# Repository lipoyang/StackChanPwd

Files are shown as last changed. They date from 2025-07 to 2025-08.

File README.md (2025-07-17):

# Stack-chan Powerd
[日本語](./README_ja.md)

Stack-chan Powerd is a M5Stack-embedded super cute humanoid controller unit.

<!-- 動画埋め込み
## Video
[![代替テキスト](https://img.youtube.com/vi/nw4zOiLLuTk/0.jpg)](https://www.youtube.com/watch?v=nw4zOiLLuTk)
 -->
## System Overview
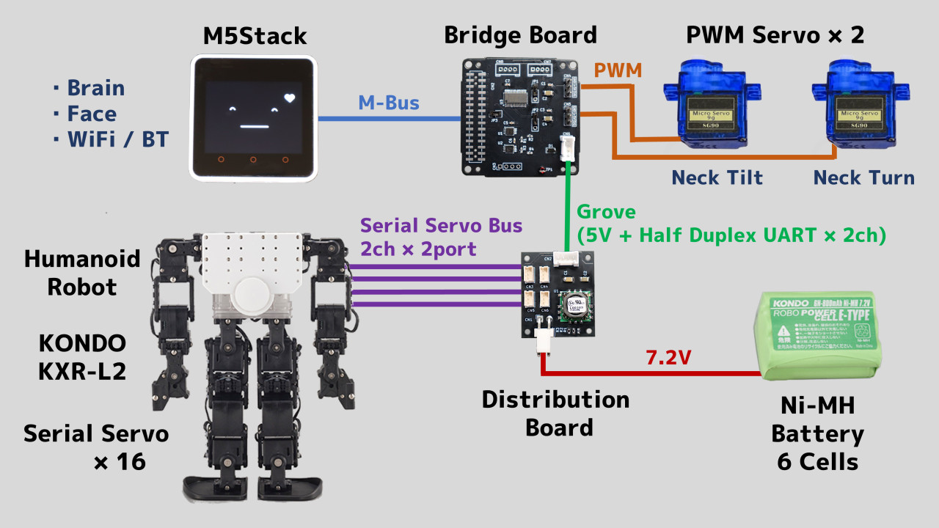
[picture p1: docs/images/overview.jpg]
System Overview


## Document
→ https://www.hackster.io/lipoyang/m5stack-as-a-humanoid-brain-b98882

## Files
* [firmware](./firmware/) : Source codes of the firmware.
* [case](./case/) : STEP and STL files of mechanical parts
* [boards](./boards/) : Schematics and PCB layout designs

## Original Work
This project is a derivative work inspired by Stack-chan. [Stack-chan](https://github.com/stack-chan/stack-chan) is the palm-sized super cute communication robot created by [Shinya Ishikawa](https://x.com/stack_chan).

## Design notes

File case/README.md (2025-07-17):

# Cumtom Mechanical Parts

These designs was forked from the original [Stack-chan case](https://github.com/stack-chan/stack-chan/tree/dev/v1.0/case).

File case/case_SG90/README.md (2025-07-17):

# Cumtom Mechanical Parts for SG90 and KXR-L2

* neck_SG90 : the neck base
* bracket_SG90_b / bracket_SG90_f : the neck bracket
* shell_SG90 : the skull shell

These designs was forked from the original [Stack-chan case](https://github.com/stack-chan/stack-chan/tree/dev/v1.0/case/case_SG90).

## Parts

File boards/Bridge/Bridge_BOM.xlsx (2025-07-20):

Reference | Qty | Part Number | Vendor | Description | DNP | Supplier | Supplier Code
C1,C3,C5,C6,C7 | 5 | 0.1uF (1608) | (generic) |  |  | - | -
C2,C4 | 2 | 100uF (3216) | (generic) |  |  | digikey | 490-GRM31CR61A107MEA8KCT-ND
CN1 | 1 | M-BUS 2x15 Pin Header (SMD) | M5Stack | M-BUS ピンヘッダ |  | スイッチサイエンス | 9591
CN2 | 1 | M-BUS 2x15 Pin Socket (SMD) | M5Stack | M-BUS ピンソケット | DNP | スイッチサイエンス | 9592
CN3 | 1 | 1x4 PinHeader | (generic) | マイク用 | DNP | - | -
CN4,CN5 | 2 | B3B-EH-A | JST | EH 3ピン (トップ型) |  | digikey | 455-B3B-EH-A-ND
CN6 | 1 | Grove (Top, through hole) | Seeed | 電源/サーボ用 |  | スイッチサイエンス | 1122
CN7,CN8 | 2 | Grove (Top, through hole) | Seeed | 拡張用 | DNP | スイッチサイエンス | 1122
D1 | 1 | SS2040FL | PANJIT |  |  | 秋月 | 102073
JP1,JP2,J3 | 3 | XX-2 | マックエイト |  |  | 秋月 | 110191
R1,R3 | 2 | 1kΩ | (generic) |  |  | - | -
R2,R4 | 2 | 100Ω | (generic) |  |  | - | -
TP1 | 1 | TEST-1 | マックエイト |  | DNP | 秋月 | 107591
U1 | 1 | 74LVC2G125DC (SM8) | TI | 0.65mm ピッチ |  | digikey | 296-SN74LVC2G125DCT3CT-ND
U2 | 1 | 74HCT2G125DP (8-TSSOP) | TI | 0.65mm ピッチ |  | digikey | 1727-3933-1-ND
U3 | 1 | PCA9685PW | NXP |  |  | digikey | 568-11925-1-ND

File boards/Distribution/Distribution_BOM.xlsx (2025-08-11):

Reference | Qty | Part Number | Vendor | Description | DNP | Supplier | Supplier Code
C1,C2 | 2 | 100uF (3216) | (generic) |  |  | digikey | 490-GRM31CR61A107MEA8KCT-ND
CN1 | 1 | B2PS-VH | JST | VH 2ピン (サイド型) |  | digikey | 455-B2PS-VH-ND
CN2 | 1 | Grove (Top, through hole) | Seeed |  |  | スイッチサイエンス | 1122
CN3,CN4,CN5,CN6 | 4 | B3B-ZR | JST | ZH 3ピン (トップ型) |  | digikey | 455-1658-ND
R1 | 1 | 1kΩ, class F | (generic) | ±1% |  | digikey | 10-ERJ-U03F1001VCT-ND
R2 | 1 | 220Ω, class F | (generic) | ±1% |  | digikey | 10-ERJ-U03F2200VCT-ND
R3 | 1 | 22Ω, class F | (generic) | ±1% |  | digikey | 10-ERJ-U03F22R0VCT-ND
U1 | 1 | OKL-T/3-W12N | Murata |  |  | digikey | 811-2072-1-ND

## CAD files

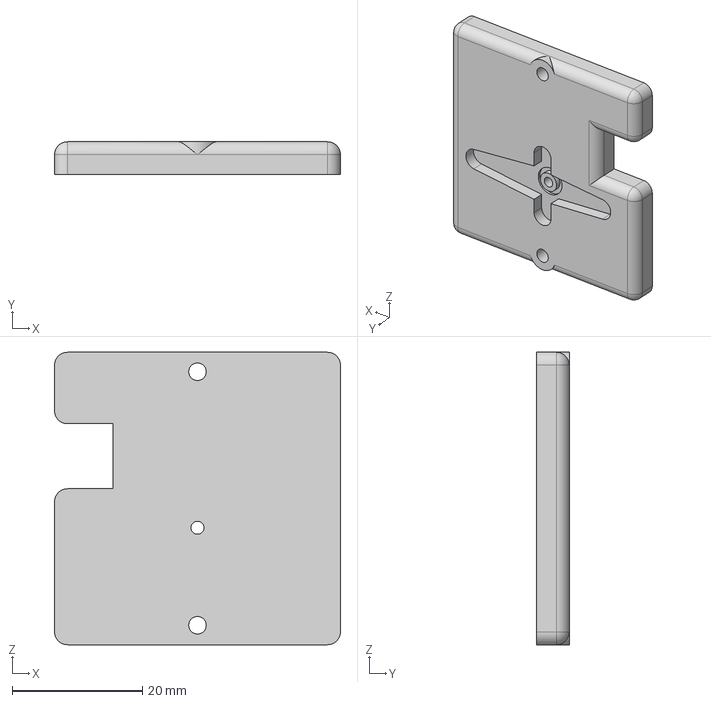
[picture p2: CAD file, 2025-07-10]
case/case_SG90/neck_SG90.step
44.0 x 5.00 x 45.0 mm

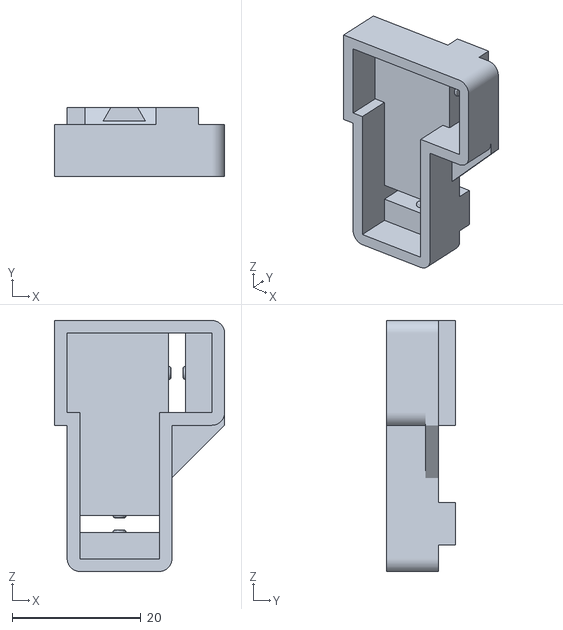
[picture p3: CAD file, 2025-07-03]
case/case_SG90/bracket_SG90_b.stl
26.5 x 10.7 x 39.1

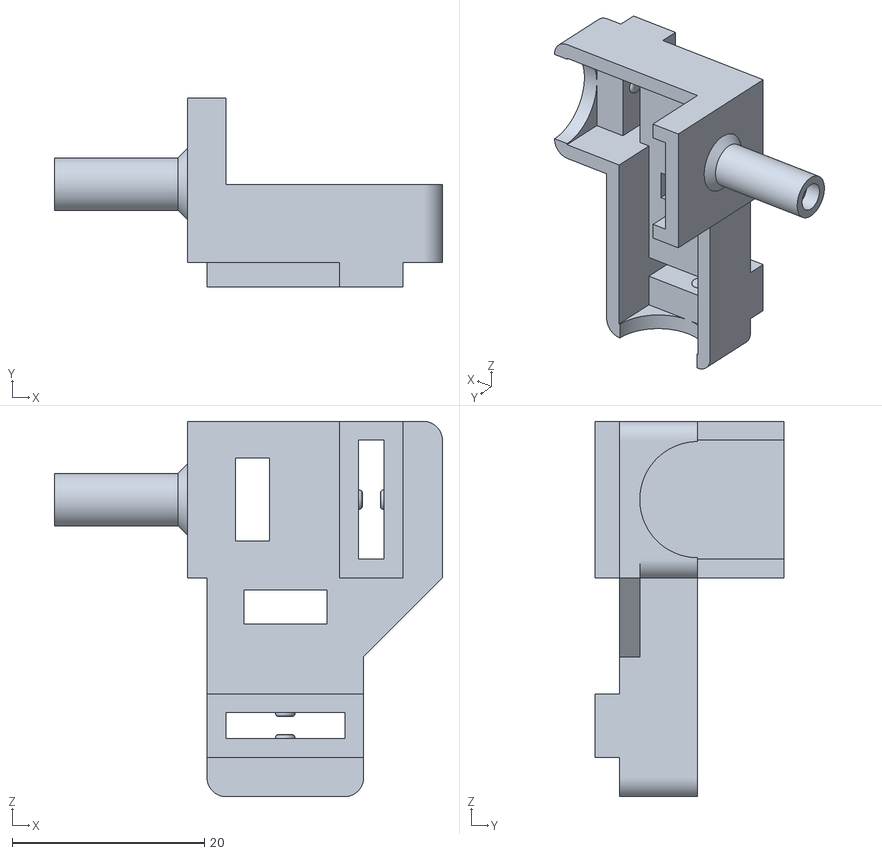
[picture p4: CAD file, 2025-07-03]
case/case_SG90/bracket_SG90_f.stl
40.4 x 19.7 x 39.1

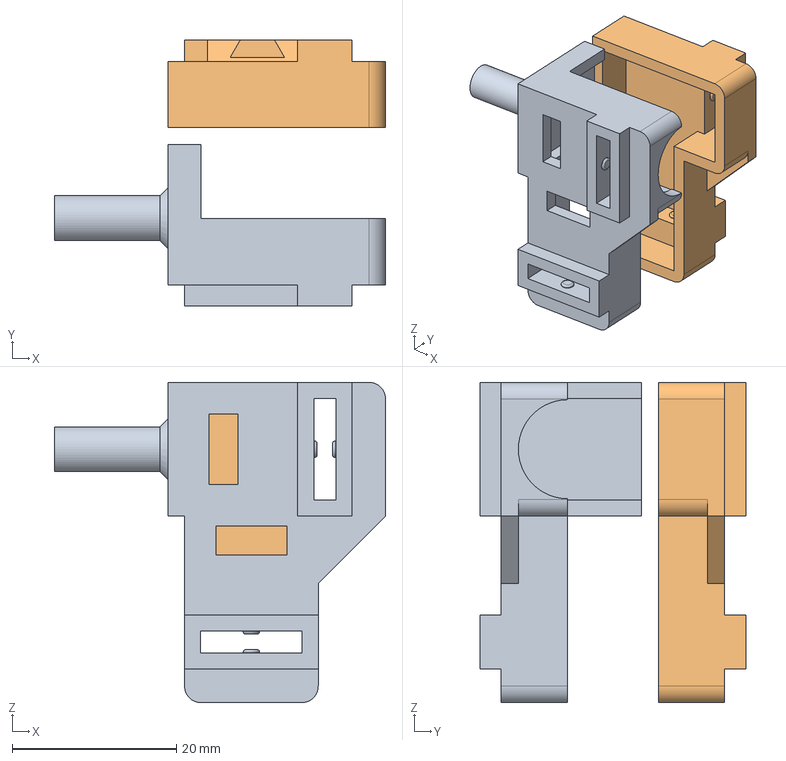
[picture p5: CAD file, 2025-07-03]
case/case_SG90/bracket_SG90.step
40.4 x 32.4 x 39.1 mm

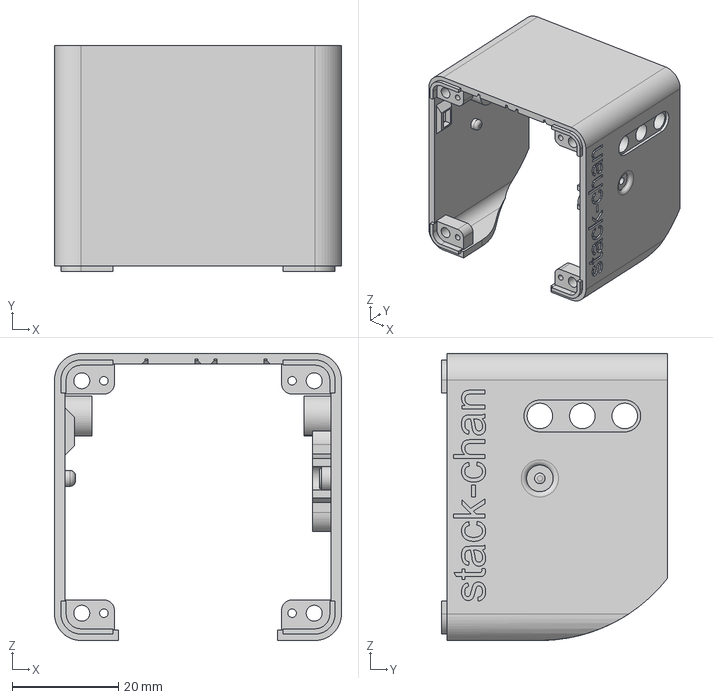
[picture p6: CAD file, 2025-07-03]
case/case_SG90/shell_SG90.step
54.0 x 42.5 x 54.0 mm

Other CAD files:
case/case_SG90/neck_SG90.stl
case/case_SG90/shell_SG90.stl

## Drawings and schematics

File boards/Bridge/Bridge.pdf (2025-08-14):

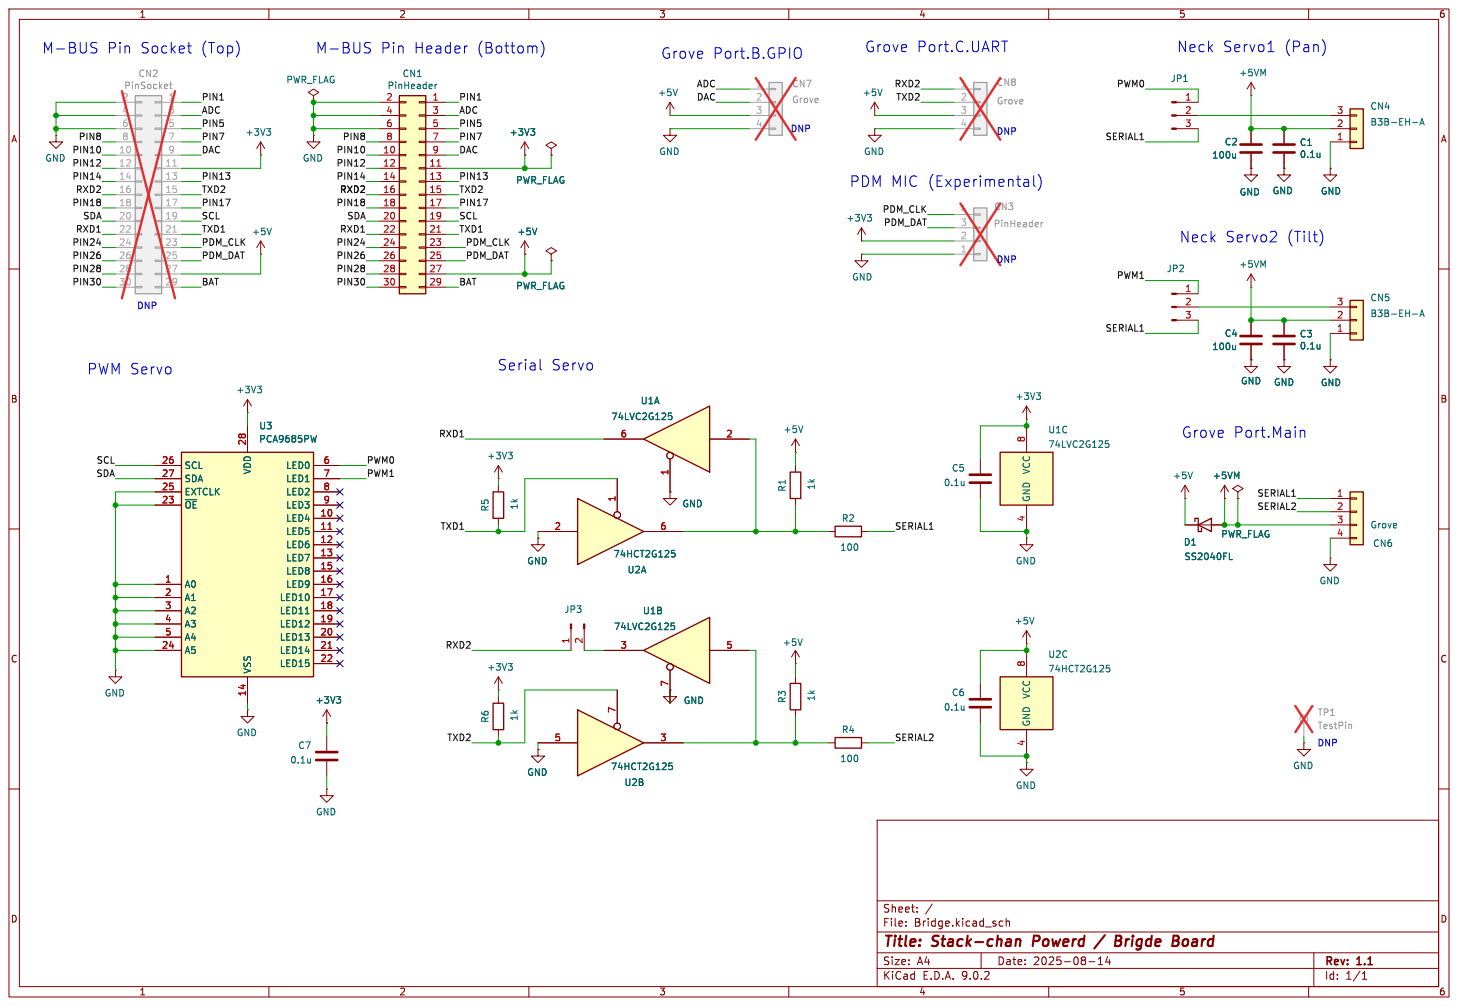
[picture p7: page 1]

M-BUS Pin Header (Bottom)

File: Bridge.kicad_sch Sheet: / GND

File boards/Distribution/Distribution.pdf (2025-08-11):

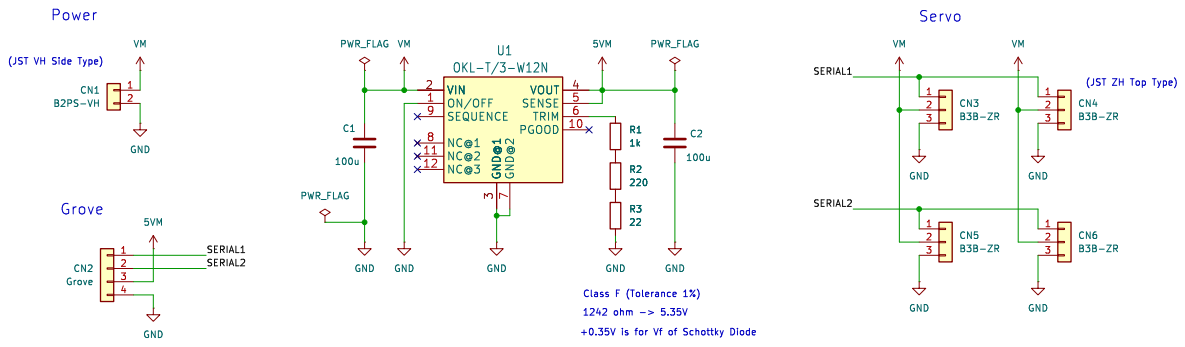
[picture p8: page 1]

(JST ZH Top Type) R3

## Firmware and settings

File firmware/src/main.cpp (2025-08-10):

#include <M5Unified.h>
#include "StackChanHead.h"
#include "GamePad_PS4.h"
#include "ICS.h"
#include "MotionController.h"
#include "Motion.h"
#include "common.h"

// シリアルポートのピン割り当て
#define PIN_RXD1 27
#define PIN_TXD1 19
#define PIN_RXD2 13
#define PIN_TXD2 14

// ICSサーボ
IcsController ics1(Serial1, PIN_RXD1, PIN_TXD1); // 右半身系統
IcsController ics2(Serial2, PIN_RXD2, PIN_TXD2); // 左半身系統
IcsServo servos[SERVO_NUM];

// モーションコントローラ
MotionController motionCtrl;

// トリム位置
const int16_t TRIM_POS[SERVO_NUM]={
//  肩P(右,左) 肩R         肘          腿R         腿P         膝           足首P       足首R
    1350,-1350,-2700,-2700,    0,    0,    0,    0, -250, -250,-2000,-2000,  520,  520,    0,    0
};

// ホームポジション
const int16_t HOME_POS[SERVO_NUM]={
//  肩P(右,左) 肩R         肘          腿R         腿P         膝           足首P       足首R
     400, -400,    0,    0,-1200,-1200,    0,    0,  150,  150,  300,  300,  150,  150,    0,    0
};

// ホームストレッチ
const uint8_t HOME_STRETCH[SERVO_NUM]={
//  肩P(右,左) 肩R         肘          腿R         腿P         膝           足首P       足首R
      20,   20,   20,   20,   65,   65,   65,   65,   65,   65,   65,   65,   65,   65,   65,   65
};

// 送信バッファ
static char txbuff[256];

// ゲームパッド (PS4コントローラ)
GamePad *gamepad;
GamePad_PS4 gamepad_ps4;
bool gamepad_connected = false;

// スタックチャン
using namespace m5avatar;
StackChanHead head;

// 初期化
void setup()
{
	auto cfg = M5.config();
  	M5.begin(cfg);

  	// スタックチャンの初期化
	head.begin();
  	head.setMicroMotion(false);

	Serial.begin(115200);
	Serial.println("StackChanPwd Start");
	
	// MACアドレスの確認用
  	uint8_t btmac[6];
  	esp_read_mac(btmac, ESP_MAC_BT);
  	Serial.printf("[Bluetooth] Mac Address = %02X:%02X:%02X:%02X:%02X:%02X\n", 
    	btmac[0], btmac[1], btmac[2], btmac[3], btmac[4], btmac[5]);

	// ICSサーボの初期化
	ics1.begin();
	ics2.begin();
	for(int i=0; i<(SERVO_NUM/2); i++){
		servos[i*2  ].attach(ics1, 1+i); // 右半身のサーボ
		servos[i*2+1].attach(ics2, 1+i); // 左半身のサーボ
	}
	
	// モーションコントローラの初期化
	motionCtrl.setServo(servos);
	motionCtrl.setTrim(TRIM_POS);
	motionCtrl.setHome(HOME_POS, HOME_STRETCH);
	motionCtrl.begin(M000::motion);

#if 0	// デバッグ用 (サーボの位置を確認)
	while(1){
		if(Serial.available() > 0){
			char c = Serial.read();
			if(c == 's') break;
		}
		for(int i=0;i<SERVO_NUM;i++){
			uint16_t pos = servos[i].getPosition();
			Serial.print(pos);Serial.print(" ");
		}
		Serial.println(" ");
		delay(1000);
	}
	Serial.println("Servo position check finished.");
#endif

	// ホームポジションに移動
	Serial.println("Stand Home position.");
	motionCtrl.standHome();

 	// ゲームパッドの初期化
	gamepad = &gamepad_ps4;
	gamepad->begin();

	// スタックチャンを居眠り状態に
	head.setBaseExpression(Expression::Sleepy);
	head.setExpression(Expression::Sleepy);
}

// メインループ
void loop()
{
	motionCtrl.loop();
	ics1.loop();
	ics2.loop();
	
	// ゲームパッド
  	if (gamepad->isConnected()) {
		if (!gamepad_connected) {
			Serial.println("GamePad connected.");
			gamepad_connected = true;
			head.setBaseExpression(Expression::Neutral);
			head.setExpression(Expression::Happy, 2000);
			head.setSpeachText("ゲームパッド接続", 2000);
			head.setMicroMotion(true);
		}
		// ゲームパッドのボタン状態を取得
		static uint32_t buttonFlag_prev = 0xFFFFFFFF;
    	uint32_t buttonFlag = gamepad->getButton();
		// ボタンフラグをモーションコントローラにセット
		motionCtrl.movButton(buttonFlag);
		if(buttonFlag != buttonFlag_prev) {
    		Serial.printf("Button Flag: 0x%08X\n", buttonFlag);
			//M5.Lcd.printf("Button Flag: 0x%08X\n", buttonFlag);
		}
		buttonFlag_prev = buttonFlag;

  	}else{
		if (gamepad_connected) {
			Serial.println("GamePad disconnected.");
			gamepad_connected = false;
			head.setBaseExpression(Expression::Sleepy);
			head.setExpression(Expression::Neutral, 2000);
			head.setSpeachText("ゲームパッド切断", 2000);
			head.setMicroMotion(false);
		}
	}

	// 開発用 (シリアル通信でのボタン入力)
	if(Serial.available() > 0){
		char c = Serial.read();
		if(c == '1') motionCtrl.setButton(BTN_L1);
		if(c == '2') motionCtrl.setButton(BTN_L2);
		if(c == '3') motionCtrl.setButton(BTN_R1);
		if(c == '4') motionCtrl.setButton(BTN_R2);
		if(c == 'a') motionCtrl.setButton(BTN_LEFT);
		if(c == 's') motionCtrl.setButton(BTN_DOWN);
		if(c == 'd') motionCtrl.setButton(BTN_UP);
		if(c == 'f') motionCtrl.setButton(BTN_RIGHT);
		if(c == 'h') motionCtrl.setButton(BTN_X);
		if(c == 'j') motionCtrl.setButton(BTN_A);
		if(c == 'k') motionCtrl.setButton(BTN_Y);
		if(c == 'l') motionCtrl.setButton(BTN_B);
		if(c == ' ') motionCtrl.clrButton(BTN_ALL);
	}
	
	// スタックチャン
	static const MotionData *motion_prev = M000::motion;
	const MotionData *motion = motionCtrl.getPresentMotion();
	if(motion != motion_prev) {
		motion_prev = motion;

		// モーションに応じてスタックチャンの表情を変える
		if((motion == M201::motion) || // パンチ左ストレート
		   (motion == M202::motion) || // パンチ右ストレート
		   (motion == M211::motion) || // A+←: パンチ左裏拳
		   (motion == M212::motion) || // A+→: パンチ右裏拳
		   (motion == M220::motion)    // A+↓: 防御
		){
			head.setExpression(Expression::Angry);
		}else{
			head.setExpression(Expression::Neutral);
		}
		// モーションに応じてスタックチャンの顔の向きを変える
		if       (motion == M003::motion) { // ←: 歩行左
			head.setPosition( 50, 0);
		} else if(motion == M004::motion) { // →: 歩行右
			head.setPosition(-50, 0);
		} else if(motion == M201::motion) {	// パンチ左ストレート
			head.setPosition( 25, 0);
		} else if(motion == M202::motion) {	// パンチ右ストレート
			head.setPosition(-25, 0);
		} else if(motion == M211::motion) { // A+←: パンチ左裏拳
			head.setPosition( 50, 0);
		} else if(motion == M212::motion) { // A+→: パンチ右裏拳
			head.setPosition(-50, 0);
		} else if(motion == M220::motion) { // A+↓: 防御
			head.setPosition(  0, -25);
		} else {
			head.setPosition(  0, 0);
		}
		// モーションに応じてスタックチャンの不随意運動を有効/無効にする
		if(motion == M000::motion){
			head.setMicroMotion(true);
		}else{
			head.setMicroMotion(false);
		}
	}
	head.loop();
}

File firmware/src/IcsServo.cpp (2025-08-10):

// KONDO ICS Serial Servo
// Based on ICS3.5

#include <stdio.h>
#include <string.h>
#include "IcsController.h"
#include "IcsServo.h"
#include "driver/uart.h" // optimize for M5Stack

/****************************************
 Constants of ICS Protocol
 ****************************************/

// CMD(command)
#define CMD_POSITION    0x80    // POSITION command
#define CMD_READ        0xA0    // READ command
#define CMD_WRITE       0xC0    // WRITE command
#define CMD_ID          0xE0    // ID command

#define CMD_MASK        0xE0    // bit mask of command
#define ID_MASK         0x1F    // bit mask of ID
#define MSB_MASK        0x7F    // bit mask of MSB

// SC(sub command) of READ/WRITE command
#define SC_EEPROM       0x00    // EEPROM
#define SC_STRETCH      0x01    // stretch
#define SC_SPEED        0x02    // speed
#define SC_CURRENT      0x03    // current
#define SC_TEMPERATURE  0x04    // temperature
#define SC_POSITION     0x05    // position (read only)

// SC(sub command) of ID command
#define SC_READ_ID      0x00    // read ID
#define SC_WRITE_ID     0x01    // write ID

// verify CMD
#define ICS_CMD_CHECK(rx, tx, tx_size) \
    ((rx[0] == tx[0]) && ((rx[tx_size+0] & MSB_MASK) == (tx[0] & MSB_MASK)))

// verify CMD (read ID command)
#define ICS_CMD_GET_ID_CHECK(rx, tx, tx_size) \
    ((rx[0] == tx[0]) && ((rx[tx_size+0] & CMD_MASK & MSB_MASK) == (CMD_ID & MSB_MASK)))

// verify SC
#define ICS_SC_CHECK(rx, tx, tx_size) \
    ((rx[1] == tx[1]) && (rx[tx_size+1] == tx[1]))

// verify DATA
#define ICS_DATA_CHECK(rx, tx, tx_size) \
    ((rx[2] == tx[2]) && (rx[tx_size+2] == tx[2]))

/****************************************
 Local Constants
 ****************************************/

// request flag bit
#define REQ_POSITION       0x01    // set & get position
#define REQ_CURRENT        0x02    // get current
#define REQ_TEMPERATURE    0x04    // get temperature

/****************************************
 Common API
 ****************************************/

// set ICS controller and servo ID
void IcsServo::attach(IcsController& controller, uint8_t id)
{
    this->controller = &controller;
    this->ID = id;
    
    // add this servo to servo chain
    if(controller.servoFirst == NULL)
    {
        controller.servoFirst = this;
        controller.servoLast = this;
        controller.servoNow = this;
    }
    else
    {
        controller.servoLast->next = this;
        controller.servoLast = this;
    }
    this->next = NULL;
}

/****************************************
 Synchronous API
 ****************************************/

// set & get position
// pos : target position
// return : current position
uint16_t IcsServo::setPosition(uint16_t pos)
{
    // command data
    uint8_t tx_data[3];
    tx_data[0] = CMD_POSITION | (ID & ID_MASK);// CMD
    tx_data[1] = (uint8_t)(pos >> 7) & 0x7F;   // POS_H
    tx_data[2] = (uint8_t)(pos & 0x7F);        // POS_L
    
    // send command and receive response
    uint8_t rx_data[3+3]={0};
    if(!this->transfer(tx_data, sizeof(tx_data), rx_data, sizeof(rx_data), 1)){
        return 0xFFFF;  // Error
    }
    
    // verify response data
    uint16_t retval;
    if(ICS_CMD_CHECK(rx_data, tx_data, 3)) // verify CMD
    {
        // current position
        retval = ((uint16_t)rx_data[3+1] << 7) | (uint16_t)rx_data[3+2];
    }else{
        retval = 0xFFFF;  // Error
    }
    return retval;
}

// read parameter (common routine)
// sc : sub command (type of parameter)
// return : value of parameter
uint8_t IcsServo::getParameter(uint8_t sc)
{
    // command data
    uint8_t tx_data[2];
    tx_data[0] = CMD_READ | (ID & ID_MASK); // CMD
    tx_data[1] = sc;  // SC
    
    // send command and receive response
    uint8_t rx_data[2+3]={0};
    if(!this->transfer(tx_data, sizeof(tx_data), rx_data, sizeof(rx_data), 1)){
        return 0xFF;  // Error
    }
    
    // verify response data
    uint8_t retval;
    if(   ICS_CMD_CHECK(rx_data, tx_data, 2) // verify CMD
       && ICS_SC_CHECK (rx_data, tx_data, 2)) // verify SC
    {
        // value of parameter
        retval = rx_data[2+2];
    }else{
        retval = 0xFF; // Error
    }
    return retval;
}

// get stretch
// return : stretch
uint8_t IcsServo::getStretch()
{
    return this->getParameter(SC_STRETCH);
}

// get speed
uint8_t IcsServo::getSpeed()
{
    return this->getParameter(SC_SPEED);
}

// get current
uint8_t IcsServo::getCurrent()
{
    return this->getParameter(SC_CURRENT);
}

// get temperature
uint8_t IcsServo::getTemperature()
{
    return this->getParameter(SC_TEMPERATURE);
}

// get position
uint16_t IcsServo::getPosition()
{
    // command data
    uint8_t tx_data[2];
    tx_data[0] = CMD_READ | (ID & ID_MASK); // CMD
    tx_data[1] = SC_POSITION;  // SC
    
    // send command and receive response
    uint8_t rx_data[2+4]={0};
    if(!this->transfer(tx_data, sizeof(tx_data), rx_data, sizeof(rx_data), 10)){
        return 0xFF;  // Error
    }
    
    // verify response data
    uint16_t retval;
    if(   ICS_CMD_CHECK(rx_data, tx_data, 2) // verify CMD
       && ICS_SC_CHECK (rx_data, tx_data, 2)) // verify SC
    {
        // value of parameter
        retval = ((uint16_t)rx_data[3+1] << 7) | (uint16_t)rx_data[3+2];
    }else{
        retval = 0xFFFF; // Error
    }
    return retval;
}


// write parameter (common routine)
// sc : sub command (type of parameter)
// value : value of parameter
// return : success or failure
bool IcsServo::setParameter(uint8_t sc, uint8_t value)
{
    // command data
    uint8_t tx_data[3];
    tx_data[0] = CMD_WRITE | (ID & ID_MASK); // CMD
    tx_data[1] = sc;    // SC
    tx_data[2] = value; // value of parameter
    
    // send command and receive response
    uint8_t rx_data[3+3]={0};
    if(!this->transfer(tx_data, sizeof(tx_data), rx_data, sizeof(rx_data), 1)){
        return false;  // Error
    }
    
    // verify response data
    bool retval;
    if(   ICS_CMD_CHECK (rx_data, tx_data, 3)  // verify CMD
       && ICS_SC_CHECK  (rx_data, tx_data, 3)  // verify SC
       && ICS_DATA_CHECK(rx_data, tx_data, 3)) // verify DATA
    {
        retval = true;
    }else{
        retval = false;
    }
    return retval;
}

// set stretch
// stretch : stretch
// return : success or failure
bool IcsServo::setStretch(uint8_t stretch)
{
    return this->setParameter(SC_STRETCH, stretch);
}

// set speed
// speed : speed
// return : success or failure
bool IcsServo::setSpeed(uint8_t speed)
{
    return this->setParameter(SC_SPEED, speed);
}

// set current limit
// current : current limit
// return : success or failure
bool IcsServo::setCurrent(uint8_t current)
{
    return this->setParameter(SC_CURRENT, current);
}

// set temperature limit
// temp : temprature limit
// return : success or failure
bool IcsServo::setTemperature(uint8_t temp)
{
    return this->setParameter(SC_TEMPERATURE, temp);
}
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

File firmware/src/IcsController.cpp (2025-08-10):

// KONDO ICS Serial Servo Controller
// Based on ICS3.5

#include <Arduino.h>
#include "IcsController.h"
#include "IcsServo.h"
#include "driver/uart.h" // optimize for M5Stack

/****************************************
 API
 ****************************************/

// constructor
// serial : serial port for ICS communication
IcsController::IcsController(HardwareSerial& serial, int rxPin, int txPin)
{
    this->serial = &serial;
    this->rxPin = rxPin;
    this->txPin = txPin;

    // optimize for M5Stack
    this->uart_num = (&serial == &Serial1) ? UART_NUM_1 : UART_NUM_2;
    
    onError = NULL;
    servoFirst = NULL;
    servoLast  = NULL;
    servoNow   = NULL;
    
    waiting = false;
}

// start ICS controller
void IcsController::begin(int baud)
{
    // ICS servo needs wait after communication
    T4 = 6*11*1000000 / baud + 400;
    
    // data 8bit, parity even, stop 1bit
    serial->begin(baud, SERIAL_8E1, rxPin, txPin);
}

// call this in main loop (for Asynchronous API)
void IcsController::loop()
{
    // ICS servo needs wait after communication
    if(waiting){
        uint32_t now = micros();
        uint32_t elapsed = now - T3;
        if((elapsed > T4)
           && (elapsed < UINT32_MAX/2)) // for GR-ROSE(beta)'s bug
        { 
            waiting = false;
        }
    }
    if(waiting) return;
    
    // if no servo, do nothing
    if(servoNow == NULL) return;
    
    // receive response
    if(servoNow->isReceiving)
    {
        servoNow->receiveAsync();
    }
    // send command
    else
    {
        // any request?
        if(servoNow->request)
        {
            servoNow->sendAsync();
            
            // ICS servo needs wait after communication
            waiting = true;
            T3 = micros();
        }
        // select next servo
        else
        {
            servoNow = (servoNow != servoLast) ? servoNow->next : servoFirst;
        }
    }
}

// requested communication completed? (for Asynchronous API)
bool IcsController::isReady()
{
    // if no servo, ready
    if(servoFirst == NULL) return true;
    
    // all servo is ready?
    for(IcsServo* servo = servoFirst; servo != NULL; servo = servo->next)
    {
        if(!servo->isReady()) return false;
    }
    return true;
}

/****************************************
 Private Functions
 ****************************************/

// get received data size
// return : received data size [byte]
int IcsController::getRxSize()
{
    return serial->available();
}

// read received data (1 byte)
// return : received data (1 byte)
uint8_t IcsController::read()
{
    return (uint8_t)(serial->read());
}

// write data to send
// data : data to send
// len : size of data to send
// return : size of sent data
int IcsController::write(uint8_t *data, int len)
{
    // discard trash data
    while(serial->available() > 0)
    {
        serial->read();
    }
    
    return serial->write(data, len);
}

// set timeout [msec]
// ms : time limit [msec]
void IcsController::setTimeout(int msec)
{
    uint32_t cnt = (uint32_t)(msec * 1000);
    T1 = micros();
    T2 = cnt;
}

// is timeout?
bool IcsController::isTimeout()
{
    uint32_t now = micros();
    uint32_t elapsed = now - T1;
    
    bool timeup = (
        (elapsed > T2)
        && (elapsed < UINT32_MAX/2) // for GR-ROSE(beta)'s bug
    );
    return timeup;
}

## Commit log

2025-06-21 add Bridge Board
    [Bridge.kicad_pcb, Bridge.kicad_sch]
2025-06-23 add Distribution board
    [Distribution.kicad_pcb, Distribution.kicad_sch]
2025-06-23 modify PCB design
    [Distribution.kicad_pcb]
2025-06-24 add BOM
    [Bridge.kicad_sch, Bridge_BOM.xlsx, Distribution.xlsx]
2025-06-24 modify PCB design for DRC
    [Bridge.kicad_pcb, Distribution.kicad_pcb]
2025-06-25 panelize PCB
    [StackChanPwd.kicad_pcb]
2025-06-28 fix PCB design
    [Bridge.kicad_pcb, Bridge.kicad_sch, Distribution.kicad_pcb]
2025-06-28 fix panelized PCB
    [StackChanPwd.kicad_pcb]
2025-06-28 add PDF and Gerber files
2025-06-28 fix PCB design (product ver1.0)
    [Bridge.kicad_pcb, StackChanPwd.kicad_pcb]
2025-07-03 add case files
    [bracket_SG90.step, bracket_SG90_b.stl, bracket_SG90_f.stl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]
2025-07-09 fix case files
    [neck_SG90 v5.step, neck_SG90 v5.stl, neck_SG90.step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]
2025-07-20 fix schematics and BOMs
    [Bridge.kicad_sch, Bridge_BOM.xlsx, Distribution.xlsx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]
2025-08-10 optimize ICS servo control
2025-08-11 fix schematic and BOM
    [Distribution.kicad_sch, Distribution_BOM.xlsx]
2025-08-14 fix Bridge Board (add pull up resistors)
    [Bridge.kicad_pcb, Bridge.kicad_sch]
2025-08-14 fix panelized PCB design
    [StackChanPwd.kicad_pcb]
